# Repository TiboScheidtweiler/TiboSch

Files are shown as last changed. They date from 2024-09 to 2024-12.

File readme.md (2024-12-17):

# LineFollower

lege repository die je als template kan gebruiken om een eigen repository te starten voor uw linefollower project

A description of my image


## specifications

microcontroller: arduino nano esp 32

motors: micro metal gear motor

h-bridge: TB6612FNG

sensors: QTR8A

batteries: 18650 litium

wireless communication: wifi

distance sensor - motors: 9 cm

weight:

speed: 0.273606

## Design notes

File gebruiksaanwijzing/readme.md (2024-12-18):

# Gebruiksaanwijzing

### opladen / vervangen batterijen
verwijder het deksel van de batterijhouder en neem de batterijen eruit. Voorzie de oplader van voeding en steek de batterijen in de oplader. Het opladen is voltooid als het lichtje groen wordt. Blijf altijd in de buurt van de batterijen tijdens het opladen voor de veiligheid.

### draadloze communicatie
#### verbinding maken
Vul in de code de naam van het wifi netwerk en het wachtwoord in. als je het programma start en op de kalibratieknop drukt zal je in de seriële monitor het IP-adres van de microcontoller kunnen uitlezen. Als je dan via je smartphone of laptop naar dit IP-adres surft via een browser kom je op een webpagina waarmee je de auto kan besturen. Let wel op dat je smartphone/laptop met hetzelfde netwerk is verbonden.

#### commando's 
- start / zorgt dat de auto begint te rijden 
- stop  / zorgt dat de auto stopt met rijden
- set power [0..255]  / bepaalt de snelheid van de auto
- set Reverse factor [o..255] / bepaalt de achterwaartse snelheid van binnenste wiel in scherpe bochten
- set kp [0..] / bepaald de kp waarde van de pid regelaar
- set ki [0..] / bepaald de ki waarde van de pid regelaar
- set kd [0..] / bepaald de kd waarde van de pid regelaar
- calibrate / de sensoren worden gekalibreert op de zwarte en witte waarden.  

### kalibratie
Druk op de kalibratieknop (pin D12) of op de kalibratie knop op de webpagina. Nu zal er 10s gekalibreert worden, de ingebouwde led zal branden zolang de kalibratie loopt. In deze 10s moeten je de sensor zwart en wit laten zien zodat de uitgelezen worden hiermee vergeleken kunnen worden. Dit zorgt voor een goede werking van de sensor.  

### settings
De robot rijdt stabiel met volgende parameters:  Kp=1,05 , Ki=0 , Kd=0,3 , Base Speed=110 , Max Speed=250 , Reverse factor=85

### start/stop button
Start/stop knop is verbonden met pin D11, maar start/stop kan ook via de webpagina. De ingebouwde led zal knipperen als de auto in de 'run' mode staat en dus zal rijden.

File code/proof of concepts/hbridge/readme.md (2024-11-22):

# H-Bridge proof of concept

minimale hard- & software + stappenplan dat aantoont dat 2 motoren onafhankelijk van elkaar kunnen draaien, en (traploos) regelbaar zijn in snelheid en draairichting.

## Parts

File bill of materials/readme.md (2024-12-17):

## bill of materials
<br />

|volgnummer|naam|omschrijving|nieuw/recup|kostprijs/stuk|aantal|subtotaal|
|---|----|---|---|---|---|---|
| 1| Arduino nano esp 32 | microcontoller | nieuw | 22,99 | 1 | 22,99 |
|2| QTR8A| sensor | nieuw | 2,09| 1|2,09|
|3| micro metal gear motor| motor|nieuw| 2,57|2| 5,15|
|4| TB6612FNG|H-brug| nieuw|3,08|1|3,08|
|5|  wiel| 43 mm D-as|nieuw|1,85|2|3,7|
|6|draaden|jumpwires 40 pack M/F 20cm|nieuw|3,98|1|3,98|
|7|breadbord| 400 punten|recup|0|0|0|
|8|frame|3D-print| nieuw|0|0|0|
|9| batterijen | 18650 litium| nieuw|3,95|2|7,89|
|10|batterijhouder|HALJIA  18650 3,7 V batterijhouder|nieuw|4,5|1|4,5|
|11|bouten + moeren| steun voorkant|nieuw|3,25|1|3,25|
|12|motorklemmen|3D-print|nieuw|0|0|0|
|13|powerswitch|schakelaar|nieuw|0|0|0|
|14|drukknoppen|drukknoppen arduino|recup|0|0|0|
|15|batterij-oplader|PowerKAN D4-26|nieuw|7,89|1|7,89|
|16|totaal|||||64,52|

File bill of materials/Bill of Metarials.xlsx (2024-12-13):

Componentenlijst | naam | prijs (€)
Microcontroller | Arduino nano esp 32 | 22.99
Sensor | QTR8A | 2.09
Motoren | micro metal gear motor 300/rpm, 6V | 5.15
H-brug | TB6612FNG | 3.08
wielen | wiel 3mm D-as -43mm | 3.7
draaden | jumpwires 40-pack-M/F-20cm | 3.98
breadbord | breadbord 400 punten | 0
frame | 3D-print | 0
batterijen | 2x 18650 litium | 7.89
batterijhouder | HALJIA 18650 3,7 V batterijhouder | 4.5
bouten + moeren | M3 x 20mm ISO 7045 | 3.25
motorklemmen | 3D-print | 0
powerswitch | schakelaar | 0
drukknoppen | drukknoppen arduino | 0
batterij-oplader | PowerKAN D4-26 | 7.89
totaal |  | 64.52

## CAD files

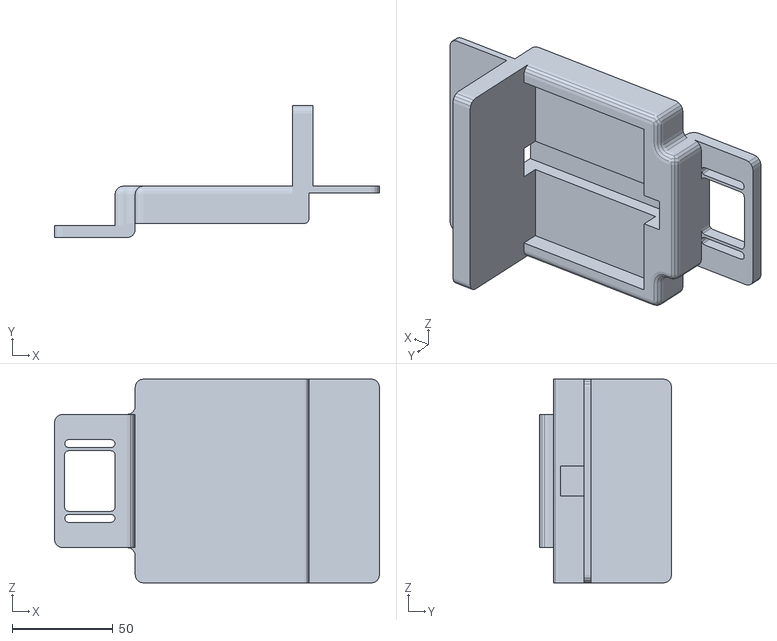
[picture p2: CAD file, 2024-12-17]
technische tekeningen/mechanisch/frame_karretje.stl
161.0 x 65.5 x 101.0

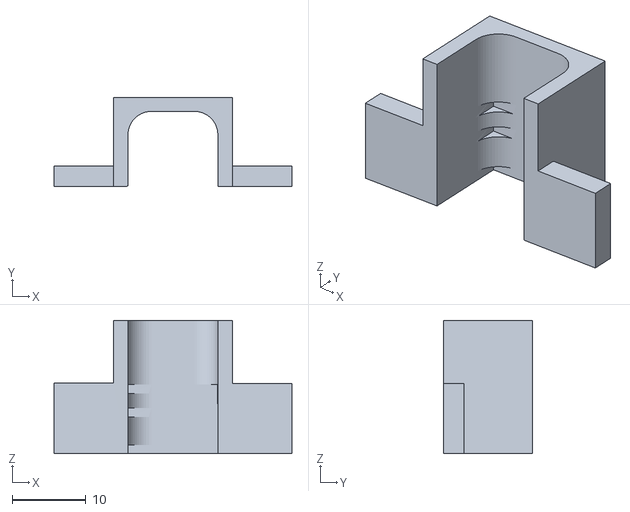
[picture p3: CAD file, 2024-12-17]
technische tekeningen/mechanisch/gearmotor_b1r_stan.stl
32.3 x 12.1 x 18.1

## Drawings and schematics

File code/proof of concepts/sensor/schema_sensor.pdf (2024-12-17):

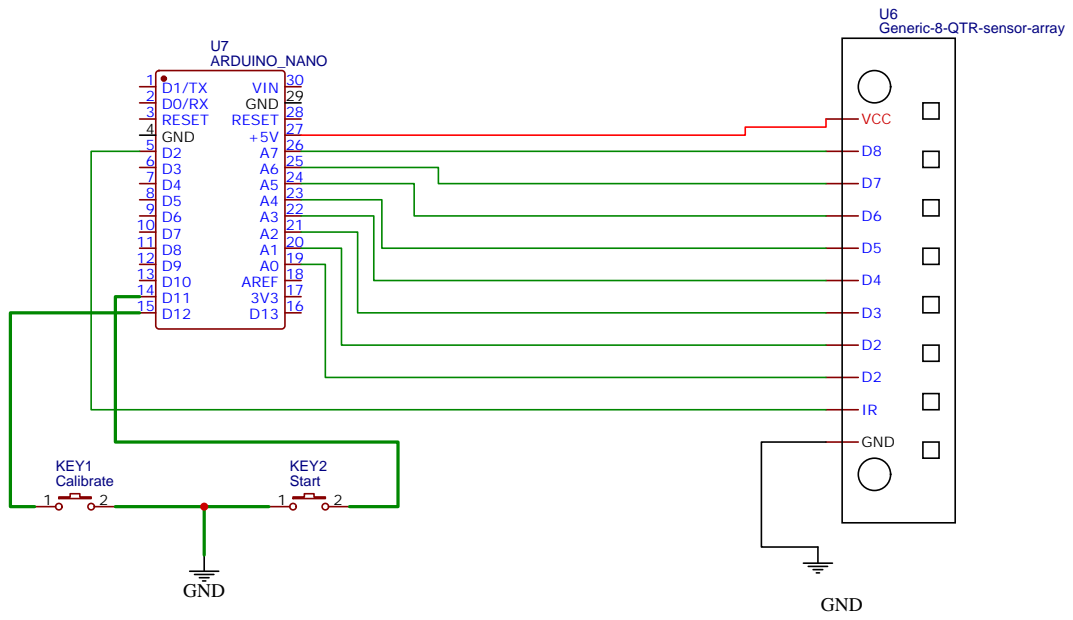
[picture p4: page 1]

Generic-8-QTR-sensor-array

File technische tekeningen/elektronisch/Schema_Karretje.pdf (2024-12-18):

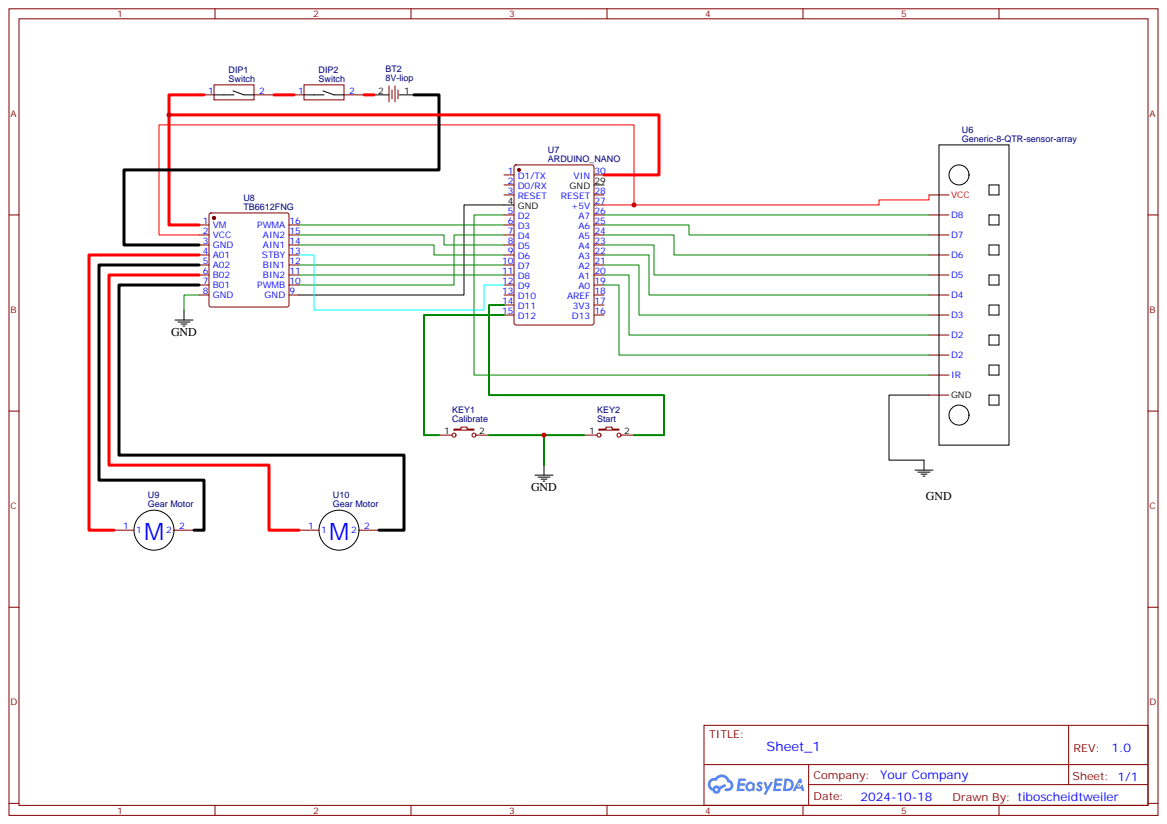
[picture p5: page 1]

Generic-8-QTR-sensor-array

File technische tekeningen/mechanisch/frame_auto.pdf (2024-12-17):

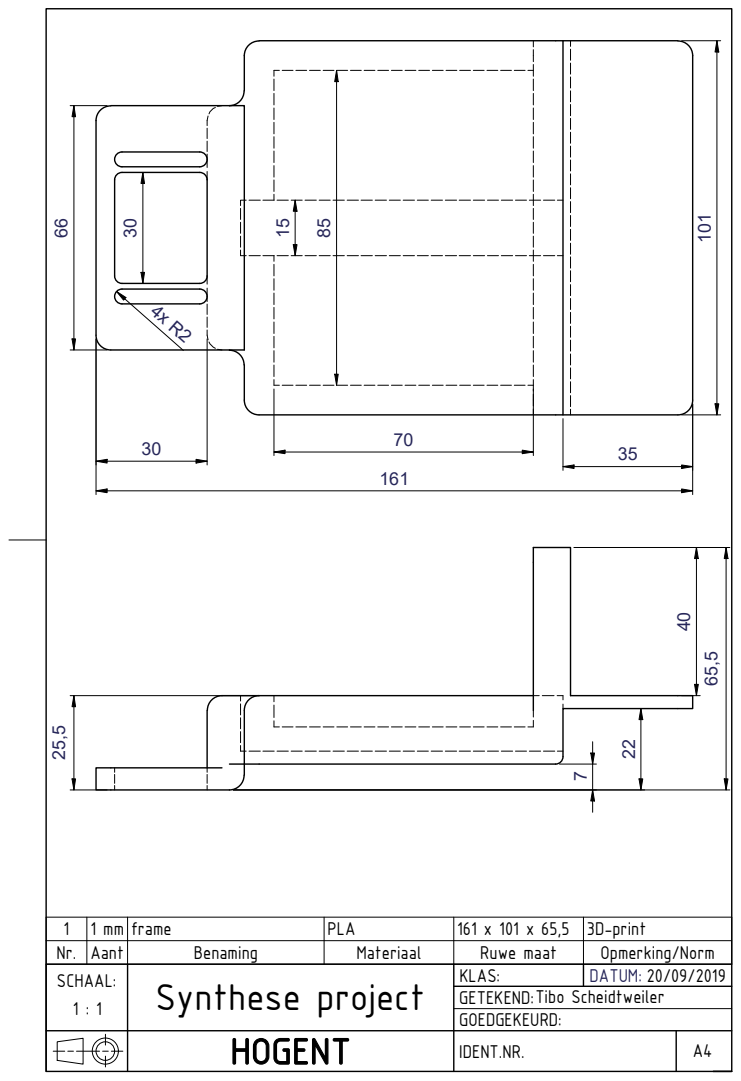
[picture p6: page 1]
DATUM: SCHAAL: Tibo Scheidtweiler

1 | 1 mm | frame | PLA | 161 x 101 x 65,5 | 3D-print
Nr. | Aant | Benaming | Materiaal | Ruwe maat | Opmerking/Norm
1 : 1 | | Synthese project | | KLAS: | 20/09/2019

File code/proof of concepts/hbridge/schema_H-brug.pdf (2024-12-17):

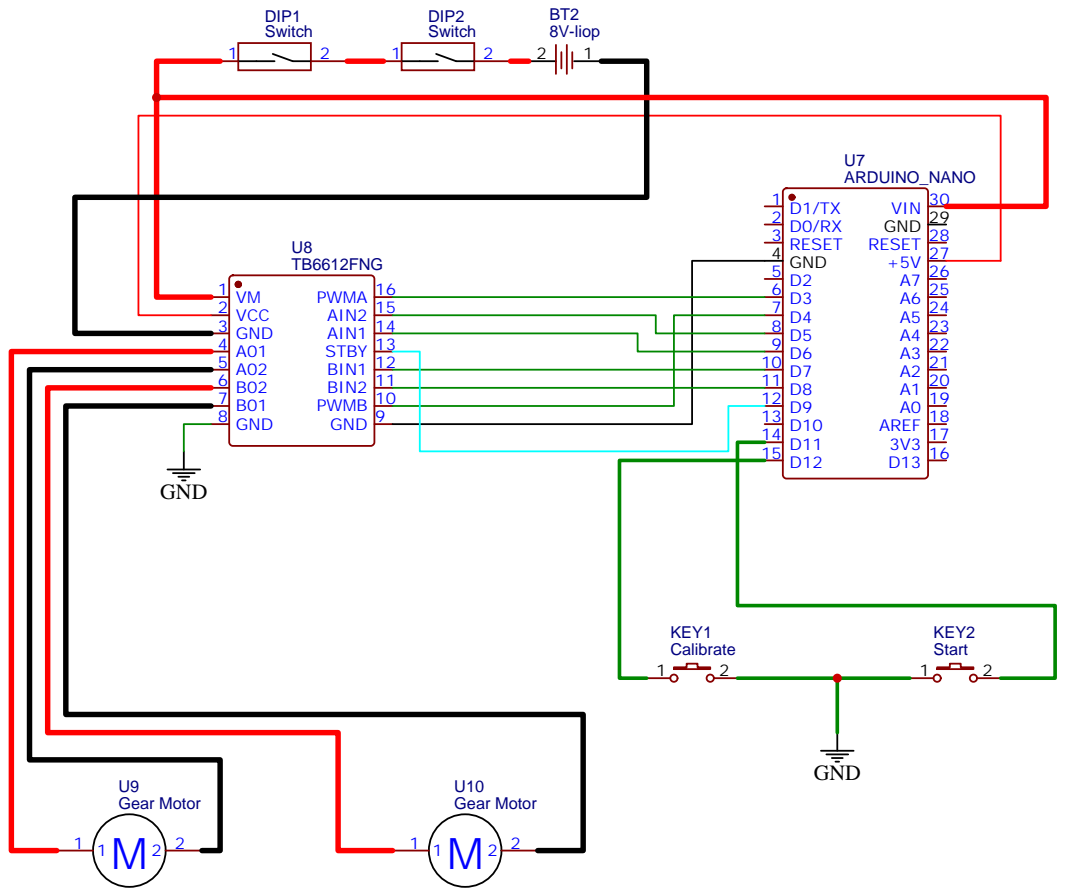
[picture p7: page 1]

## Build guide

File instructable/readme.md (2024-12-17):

# Instructable

Een instructable is een stappenplan - zonder verdere uitleg - hoe je vertrekkend van de bill of materials en gebruik makend van de technische tekeningen de robot kan nabouwen. Ook de nodige stappen om de microcontroller te compileren en te uploaden staan beschreven.  

### stap 1
bestel alle componenten uit de bill of materials  
### Stap 2:  chasis montage
- Lijm de motoren vast vanachter aan het chasis met de motorklemmen. Soldeer de aansluitdraden aan de motoren en steek door de gleuf achteraan.
- Bevestig de sensor vooraan het frame doormiddel van 2 M3 bouten en moeren. Om de sensor op de juiste hoogte te hangen kan je door hetzelfde gat nog een bout steken met langs beide kanten een moer zodat de kop van de bout verder uitsteekt dan de sensoren. Verbind met M/F kabels om naar het breadbord te gaan.
- Lijm de batterijhouder vast boven de wielen. Zorg dat je het deksel nog kan verwijderen.
- Lijm het breadbord vast in het middenste vak. Op het breadbord steek je de microcontoller en de H-brug. Zorg ook voor een kalibratie knop en een start/stop knop.
- Monteer de wielen op de motorassen
### Stap 3: elektrische aansluitingen
- Soldeer de positieve kant van de batterij-aansluiting aan de powerswitch. En sluit de batterij aan de H-brug en de Vin pin van de microcontroller. Zorg dat alle ground pinnen met elkaar verbonden staan.
- Sluit de motoren aan op de H-brug.
- Volg voor de andere aansluitingen het elektrisch schema.
### Stap 4: Software instaleren
- Installeer Arduino IDE.
- ESP32 configureren in Arduino IDE:
- Open de Arduino IDE.
- Ga naar Tools > Board > Board Manager en installeer de ESP32-bibliotheek.
-Installeer ook de QTR 8A bibliotheek en de wifi bibliotheek.
### Stap 5: Code uploaden
Om de code te uploaden moet je de microcontroller in upload mode brengen. Dit doe je door dubbel te klikken op de reset knop, als de RGB led alle kleuren afgaat, druk je nog eens. Nu zou de led groen moeten knipperen. Dan kan je de juiste COM poort aanduiden in de programmeer omgeving en uploaden. 
Na het uploaden klik je nog eens op de reset knop en trek je de microcontroller uit en steek je hem terug in. Als de Arduino is opgestart klik je nog eens reset. Dan zou het programma moeten draaien.
### Stap 6: wireless communication
- Door in de seriële monitor te kijken kan je het IP-adres zien
- Surf naar dit IP-adres.
### Stap 7: Functionele Test
- Sluit de batterij aan op de batterijhouders.
- Plaats de robot op het zwarte vlak en calibreer, plaat de robot na 5sop wit.
- Plaats de robot op het parcour en druk start.
- Controleer of de robot de lijn correct volgt.

Je linefollower robot is nu klaar!

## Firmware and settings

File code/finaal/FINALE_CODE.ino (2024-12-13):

#include <QTRSensors.h>
#include <WiFi.h>
#include <WebServer.h>

// WiFi credentials
const char* ssid = "iotroam";
const char* password = "LDgsdJd8";

WebServer server(80); // Webserver op poort 80

// QTR-8A sensor setup
QTRSensors qtr;

const uint8_t SensorCount = 8;
uint16_t sensorValues[SensorCount];

// Motor driver pins
const int PWMA = 3;  // Left motor PWM
const int AIN1 = 6;  // Left motor direction
const int AIN2 = 5;  // Left motor direction

const int PWMB = 4;  // Right motor PWM
const int BIN1 = 7;  // Right motor direction
const int BIN2 = 8;  // Right motor direction

const int STBY = 9;  // Standby pin

// Physical button pins
const int START_STOP_BUTTON = 12;  // Start/Stop button
const int CALIBRATE_BUTTON = 11;   // Calibration button

// LED pin
const int STATUS_LED = LED_BUILTIN;

// PID constants
float Kp = 1.05;
float Ki = 0.0;
float Kd = 0.0;

int baseSpeed = 120;  // Base speed for the motors
int maxSpeed = 250;   // Maximum motor speed
float reverseFactor = 85; // Factor for reverse speed in tight turns

float lastError = 0;
float integral = 0;

bool isRunning = false;  // Start knop status
unsigned long lastBlinkTime = 0;  // Voor LED-knipperen
bool ledState = false;  // Status van knipperende LED

void setup() {
  // Sensor setup
  Serial.begin(115200);
  
  qtr.setTypeAnalog();
  qtr.setSensorPins((const uint8_t[]){A0, A1, A2, A3, A4, A5, A6, A7}, SensorCount);
  qtr.setEmitterPin(2);

  pinMode(PWMA, OUTPUT);
  pinMode(AIN1, OUTPUT);
  pinMode(AIN2, OUTPUT);

  pinMode(PWMB, OUTPUT);
  pinMode(BIN1, OUTPUT);
  pinMode(BIN2, OUTPUT);

  pinMode(STBY, OUTPUT);
  digitalWrite(STBY, HIGH);  // Enable motor driver

  pinMode(START_STOP_BUTTON, INPUT_PULLUP);  // Start/Stop button
  pinMode(CALIBRATE_BUTTON, INPUT_PULLUP);   // Calibration button
  pinMode(STATUS_LED, OUTPUT);  // Status LED

  // WiFi verbinding
  WiFi.begin(ssid, password);
  while (WiFi.status() != WL_CONNECTED) {
    delay(500);
    Serial.print(".");
  }
  Serial.println("Connected to WiFi!");
  Serial.print("IP-adres: ");
  Serial.println(WiFi.localIP());

  // Webserver routes
  server.on("/", handleRoot);
  server.on("/update", handleUpdate);
  server.on("/start", handleStart);
  server.on("/calibrate", handleCalibrate);
  server.begin();
  Serial.println("Server started");
}

void loop() {
  server.handleClient();

  // Check physical buttons
  if (digitalRead(START_STOP_BUTTON) == LOW) {
    delay(50);  // Debounce
    if (digitalRead(START_STOP_BUTTON) == LOW) {
      isRunning = !isRunning;
      while (digitalRead(START_STOP_BUTTON) == LOW) {
        delay(10);  // Wait until button is released
      }
    }
  }

  if (digitalRead(CALIBRATE_BUTTON) == LOW) {
    delay(50);  // Debounce
    if (digitalRead(CALIBRATE_BUTTON) == LOW) {
      calibrateSensors();
      while (digitalRead(CALIBRATE_BUTTON) == LOW) {
        delay(10);  // Wait until button is released
      }
    }
  }

  if (isRunning) {
    uint16_t position = qtr.readLineBlack(sensorValues);
    float error = position - 3500;
    integral += error;
    float derivative = error - lastError;
    float output = Kp * error + Ki * integral + Kd * derivative;
    lastError = error;

    int leftSpeed = baseSpeed + output;
    int rightSpeed = baseSpeed - output;

    // Controleer of een wiel achteruit moet draaien
    if (leftSpeed < 0) {
      leftSpeed *= reverseFactor;  // Toepassen van reverseFactor
    }
    if (rightSpeed < 0) {
      rightSpeed *= reverseFactor;  // Toepassen van reverseFactor
    }

    // Snelheden beperken
    leftSpeed = constrain(leftSpeed, -maxSpeed, maxSpeed);
    rightSpeed = constrain(rightSpeed, -maxSpeed, maxSpeed);

    setMotor(leftSpeed, rightSpeed);

    // LED knipperen tijdens run
    unsigned long currentTime = millis();
    if (currentTime - lastBlinkTime >= 500) {
      ledState = !ledState;
      digitalWrite(STATUS_LED, ledState);
      lastBlinkTime = currentTime;
    }
  } else {
    setMotor(0, 0);  // Stop motors
    digitalWrite(STATUS_LED, LOW);  // LED uit als niet aan het runnen
  }

  delay(10);
}

void setMotor(int leftSpeed, int rightSpeed) {
  if (leftSpeed > 0) {
    digitalWrite(AIN1, HIGH);
    digitalWrite(AIN2, LOW);
    analogWrite(PWMA, leftSpeed);
  } else {
    digitalWrite(AIN1, LOW);
    digitalWrite(AIN2, HIGH);
    analogWrite(PWMA, -leftSpeed);
  }

  if (rightSpeed > 0) {
    digitalWrite(BIN1, HIGH);
    digitalWrite(BIN2, LOW);
    analogWrite(PWMB, rightSpeed);
  } else {
    digitalWrite(BIN1, LOW);
    digitalWrite(BIN2, HIGH);
    analogWrite(PWMB, -rightSpeed);
  }
}

void calibrateSensors() {
  Serial.println("Calibrating...");
  digitalWrite(STATUS_LED, HIGH);  // LED continu aan tijdens kalibratie
  for (uint16_t i = 0; i < 400; i++) {
    qtr.calibrate();
    delay(10);
  }
  digitalWrite(STATUS_LED, LOW);  // LED uit na kalibratie
  Serial.println("Calibration done!");
}

void handleRoot() {
  server.send(200, "text/html", 
    "<html>"
    "<body>"
    "<h1>PID Control Panel</h1>"
    "<form action='/update'>"
    "Kp: <input type='text' name='Kp' value='" + String(Kp) + "'><br>"
    "Ki: <input type='text' name='Ki' value='" + String(Ki) + "'><br>"
    "Kd: <input type='text' name='Kd' value='" + String(Kd) + "'><br>"
    "Base Speed: <input type='text' name='baseSpeed' value='" + String(baseSpeed) + "'><br>"
    "Max Speed: <input type='text' name='maxSpeed' value='" + String(maxSpeed) + "'><br>"
    "Reverse Factor: <input type='text' name='reverseFactor' value='" + String(reverseFactor) + "'><br>"
    "<input type='submit' value='Update'>"
    "</form>"
    "<a href='/start'>Start/Stop</a><br>"
    "<a href='/calibrate'>Calibrate</a>"
    "</body></html>");
}

void handleUpdate() {
  if (server.hasArg("Kp")) Kp = server.arg("Kp").toFloat();
  if (server.hasArg("Ki")) Ki = server.arg("Ki").toFloat();
  if (server.hasArg("Kd")) Kd = server.arg("Kd").toFloat();
  if (server.hasArg("baseSpeed")) baseSpeed = server.arg("baseSpeed").toInt();
  if (server.hasArg("maxSpeed")) maxSpeed = server.arg("maxSpeed").toInt();
  if (server.hasArg("reverseFactor")) reverseFactor = server.arg("reverseFactor").toFloat();
  server.send(200, "text/html", "Parameters updated! <a href='/'>Back</a>");
}

void handleStart() {
  isRunning = !isRunning;
  server.send(200, "text/html", String(isRunning ? "Started" : "Stopped") + " <a href='/'>Back</a>");
}

void handleCalibrate() {
  calibrateSensors();
  server.send(200, "text/html", "Calibration done! <a href='/'>Back</a>");
}

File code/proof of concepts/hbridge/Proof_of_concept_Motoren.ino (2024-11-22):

#include <SparkFun_TB6612.h>

#include <SparkFun_TB6612.h>

//motor A
int pwmA = 3;
int in1A = 6;
int in2A = 5;

//motor B
int pwmB = 4;
int in1B = 7;
int in2B = 8;


int motorSpeed1 = 0;
int motorSpeed2 = 0;



void setup() {
  // put your setup code here, to run once:

  pinMode(pwmA,OUTPUT);
  pinMode(in1A,OUTPUT);
  pinMode(in2A,OUTPUT);
  pinMode(pwmB,OUTPUT);
  pinMode(in1B,OUTPUT);
  pinMode(in2B,OUTPUT);

  Serial.begin(9600);
  delay(500);
}

void loop() {
  // put your main code here, to run repeatedly:

  digitalWrite(in1A,LOW);
  digitalWrite(in2A,HIGH);

  analogWrite(pwmA,motorSpeed1);

  if (motorSpeed1 < 230)
  {
    motorSpeed1 = motorSpeed1 +20;
    Serial.println(motorSpeed1);
    
  }

  delay(2000);
}

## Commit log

2024-11-22 Update readme.md
    Code sensor
2024-11-22 Add files via upload
    aansluitschema H-brug + sensor
2024-11-22 Add files via upload
    code motoren
2024-11-23 Add files via upload
    wireless communication via wifi met esp32
